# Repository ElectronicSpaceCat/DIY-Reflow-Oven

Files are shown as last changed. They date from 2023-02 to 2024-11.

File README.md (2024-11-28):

# DIY-Reflow-Oven
Firmware for running a PID controlled reflow oven

The toaster oven used in this project was the Black & Decker TO1785SG.

I was inpsired to make this project when I came across the https://www.rocketscream.com/blog/product/tiny-reflow-controller-v2/ controller while looking for a simple solution to building an oven myself.

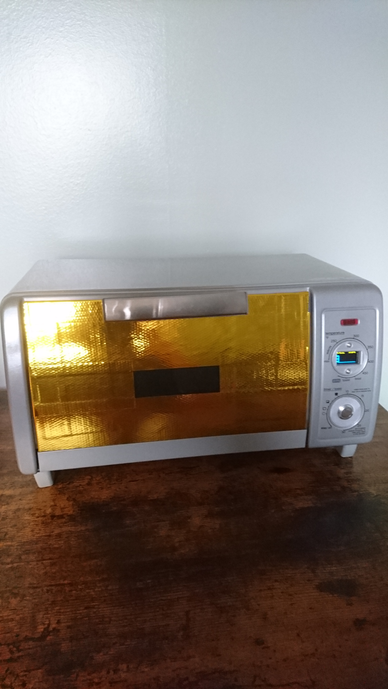
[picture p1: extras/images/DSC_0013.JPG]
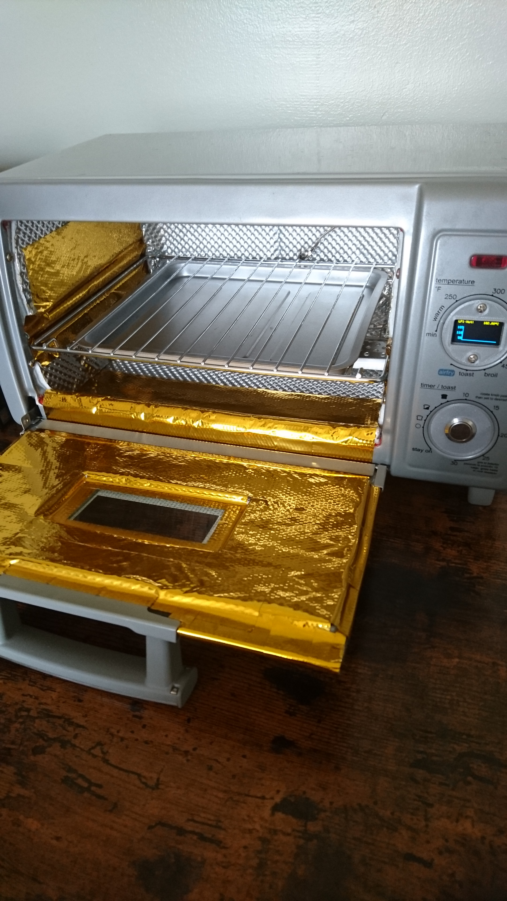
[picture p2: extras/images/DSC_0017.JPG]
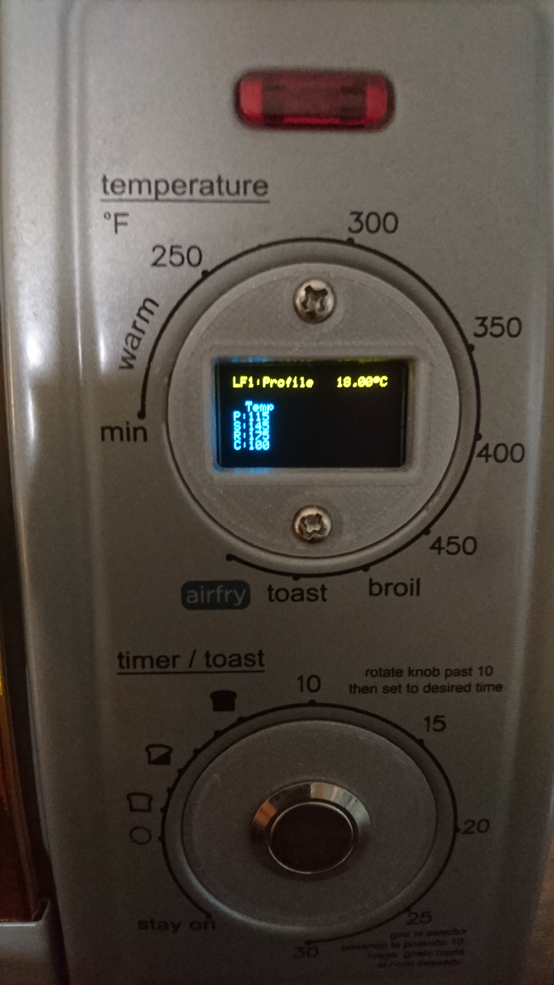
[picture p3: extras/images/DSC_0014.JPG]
  

Unfortunately the controllers were out of stock at the time so I ordered some of the parts like the OLED screen and SSRs to design my own implementation.

I chose to use an Arduino Mega 2560 Rev3 that I had laying around (finally had a use for it) and I wrote the firmware in C/C++ in Eclipse. I used a makefile from a Nordic nRF52 project to build it (to be independent of any IDE used). Note: The makefile will need to be modified depending on where your source files are located.

This reflow oven design has a single button for accessing/selecting reflow profiles and returning to the main screen.

A few toaster build guides:  
https://www.rocketscream.com/blog/forums/topic/reflow-oven-builds/  
https://www.whizoo.com/reflowoven

## Tools Needed
* Dremel or something to cut holes in the toaster
* 3d printer for the face plates

## Parts Used
* 1x Arduino Mega 2560 Rev3 (could likely port to other versions)  
https://store.arduino.cc/products/arduino-mega-2560-rev3

* 1x TO1785SG Toaster  
https://www.amazon.com/BLACK-DECKER-TO1785SG-Toaster-4-Slice/dp/B08R7WCRT8/ref=cm_cr_arp_d_product_top?ie=UTF8

* 1x Adafruit MCP9600  
https://www.amazon.com/Adafruit-4101-MCP9600-Thermocouple-Amplifier/dp/B07SZ8YVTW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

* 1x Alligator Clip K-Type Thermocouple Thermometer  
https://www.amazon.com/GenieFun-Alligator-Thermocouple-Thermometer-Temperature/dp/B01N11I90O

* 1x 6AN Weld on Bung Fitting (optional, but was used to run the thermocouple through the wall to the electronics side)  
https://www.amazon.com/EVIL-ENERGY-Fitting-Adapter-Stainless/dp/B089VP476L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

* 1x 7/16-20 Hex Jam Nut (for the weld bung)
https://www.amazon.com/16-20-Fine-Thread-Stainless-Steel/dp/B07QHFX87J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

* 1x Momentary Push Button Switch High Round Cap Waterproof Stainless Steel  
https://www.amazon.com/Waterproof-Momentary-Stainless-Button-Terminals/dp/B079HTQ7XD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

* 1x OLED 128x64 Pixel  
https://www.amazon.com/Hosyond-Display-Self-Luminous-Compatible-Raspberry/dp/B09C5K91H7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

* 3x SSR-40 AA (Kinda cheap (had a terminal break off), may want something better)  
1x each for the bottom element, top element, and fan (optional)  
https://www.amazon.com/SSR-40AA-80-250V-Output-24-380V-SSR-40/dp/B07FVDL7YX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

* 9VDC 1A Arduino Compatible Power Supply Adapter 110V AC (barrel jack needs to be cut off)
https://www.amazon.com/dp/B018OLREG4?th=1&psc=1&language=en_US

* Quick Connects (These things are amazing)  
https://www.amazon.com/Connectors-Conductor-Combination-Assortment-Connection/dp/B09CKDWK4Q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

* Reflect-A-GOLD   
https://www.designengineering.com/reflect-a-gold-heat-reflective-tape-2-x-15/

* Floor & Tunnel Shield II   
https://www.designengineering.com/floor-tunnel-shield-ii-21-x-24/

* Temperature Silicone Sealant   
https://www.amazon.co.uk/Weld-31314-Temperature-Silicone-Sealant/dp/B00ID8IUJY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

## Arduino Pinout
Refere to: ``` ./src/reflow_system.h ```

## How to use
* A short press at the main screen will start the reflow cycle. The temperature will be graphed over time and a vertical marker will indicated when it's in the next zone.
* Long press the button at the main screen to access the profile selecton screen. Once there, quick presses will cycle 1 of 5 hardcoded profiles.
Profiles can be modified in: ``` ./src/reflow_profiles.cpp ```
* Long press again to return to the main screen.
* Short press anytime during a cycle will abort it

## Screen Legend
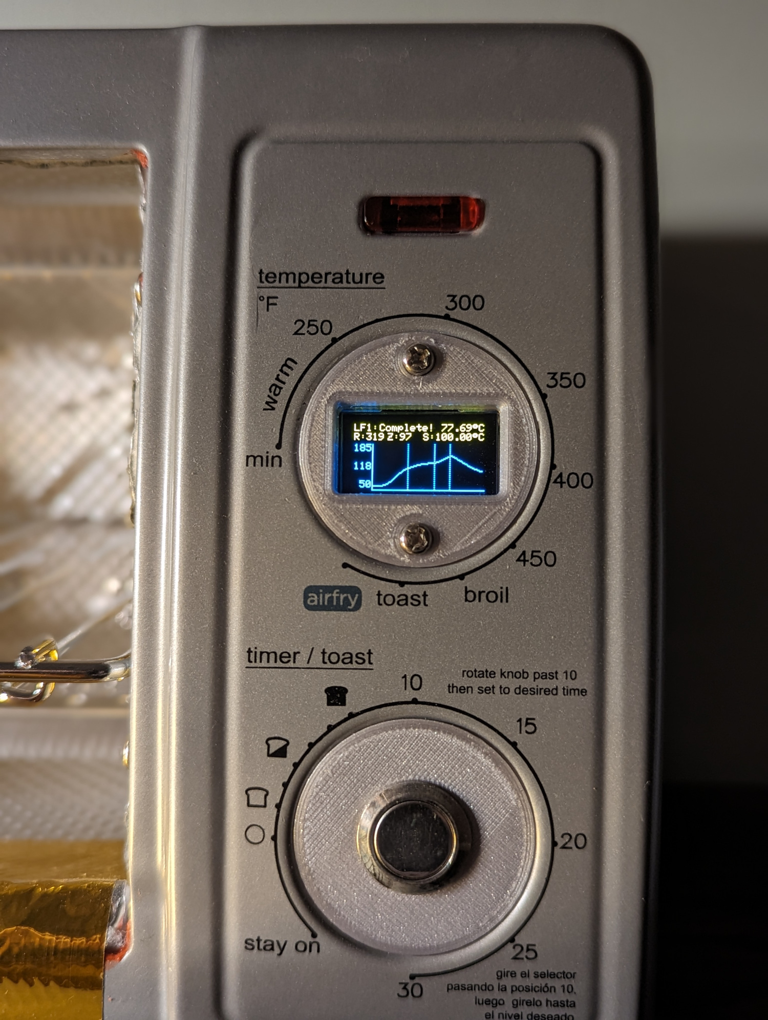
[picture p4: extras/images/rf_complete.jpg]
`  

From top left to top right (first line)  
<pre>
LF1       -  Lead Free Profile 1 (can modify but should keep it to 3 characters)  
Preheat   -  One of the states in: */src/reflow_state_machine.h >> state_t  
--.--C    -  Temperature read by the thermocouple  
</pre>

From bottom left to bottom right (second line)  
<pre>
R:--      -  Reflow time in seconds  
Z:--      -  Zone time in seconds  
S:---.--C -  Temperature setpoint for current zone
</pre>

## Compiling
#### Windows/Linux
* MinGW required for Windows to build, install instructions here: https://www.geeksforgeeks.org/installing-mingw-tools-for-c-c-and-changing-environment-variable/)
* Download the arm sdk to the project root folder from: https://developer.arm.com/downloads/-/gnu-rm
  * Windows: ```gcc-arm-none-eabi-10.3-2021.10-win32.zip```
  * Linux 32bit: ```gcc-arm-none-eabi-10.3-2021.10-x86_64-linux.tar.bz2```
  * Linux 64bit: ```gcc-arm-none-eabi-10.3-2021.10-aarch64-linux.tar.bz2```
* Clone to project root folder: https://github.com/arduino/ArduinoCore-sam.git
* Clone to project root folder: https://github.com/arduino/arduino-flash-tools.git
* Open command terminal: ```cd (path location here)/diy-reflow-oven```
* Run ```make```

  #### Update the following paths if needed:
  * ```./Makefile```:
    ```
    SDK_ROOT := $(PROJ_DIR)/ArduinoCore-sam
    SDK_TOOLS_ROOT := $(PROJ_DIR)/ArduinoCore-sam/packages/arduino/tools
    LINKER_DIR := $(SDK_ROOT)/variants/arduino_due_x/linker_scripts/gcc
    GNU_INSTALL_ROOT := $(PROJ_DIR)/gcc-arm-none-eabi-10.3-2021.10/bin/
    ```

## Flashing Firmware
  #### Windows
  * Run ```./usb_flash.bat``` and make sure to replace ```COM4``` with the correct port at the line  ```COMM_PORT := COM4```
  * The executable location in ```./usb_flash.bat``` can be modified at the line:
    ```
    $(PROJ_DIR)\arduino-flash-tools\tools_windows\bossac\bin
    ```
  #### Linux
  * Make sure the script is executable with ```sudo chmod +x usb_flash.sh```
  * Run ```./usb_flash.sh``` and make sure to replace ```ttyACM1``` with the correct port at the line ```COMM_PORT=ttyACM1```
  * Typically the port should be on ```ttyACM0``` or ```ttyACM1```
  * The executable location in ```./usb_flash.sh``` can be modified at the line:
    ```
    $(PROJ_DIR)\arduino-flash-tools\tools_linux_64\bossac\bin
    ```
  #### Notes
  * Precompiled binaries are also available at ```./build```
  * If the Adruino binary drag and drop flash method isn't broken like mine was then you may try that option instead.

## Debug/Testing
* Use a program like Putty to connect to the Arduino over USB at 115200 baud rate.  
* Type "help" to get a list of available commands.
* PID Tuning: Replace reflow_main.cpp with pid_tuner.cpp and recompile. Type "help" for available commands.
* The PID tuner is separate because it wasn't meant for reflow purposes. It was for recording the temperature ramp rates from room temp to the setpoint. Sadly, I lost spreadsheet with some of my test data. However, one can set Putty to record the output window and save it as a csv file, which the debug output is already formatted for it.

## TODO
* schematic
* more images

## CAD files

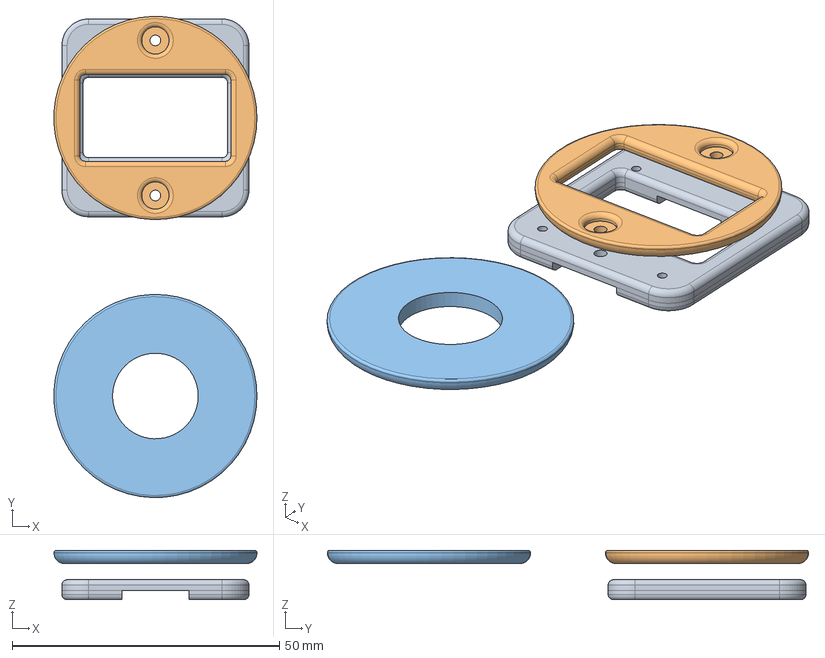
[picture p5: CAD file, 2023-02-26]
extras/cad/FreeCad/covers.FCStd
38.0 x 90.0 x 9.25 mm

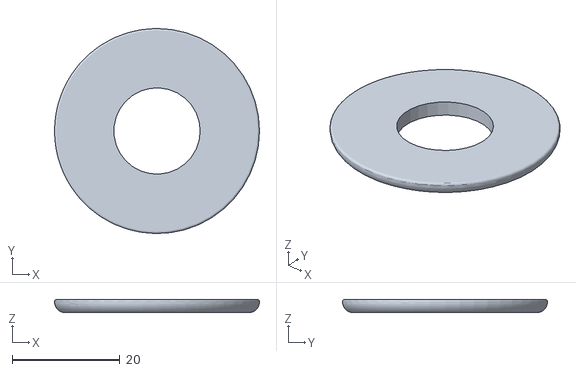
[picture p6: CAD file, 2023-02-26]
extras/cad/FreeCad/button_cover.obj
38.0 x 38.0 x 2.50

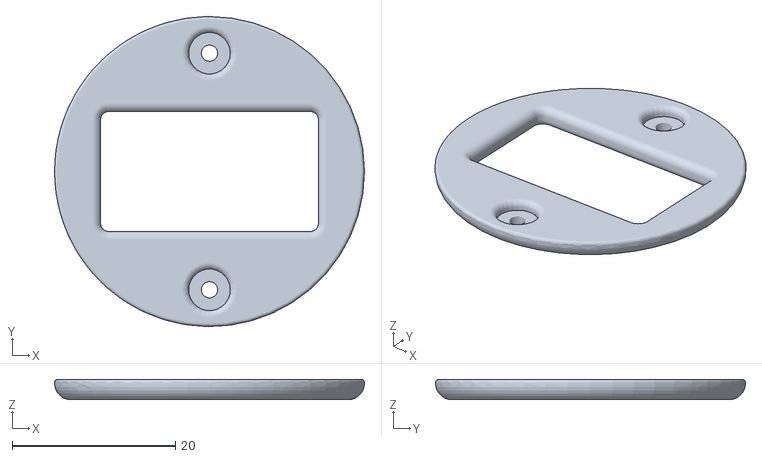
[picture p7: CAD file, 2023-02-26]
extras/cad/FreeCad/oled_front.obj
38.0 x 38.0 x 2.50

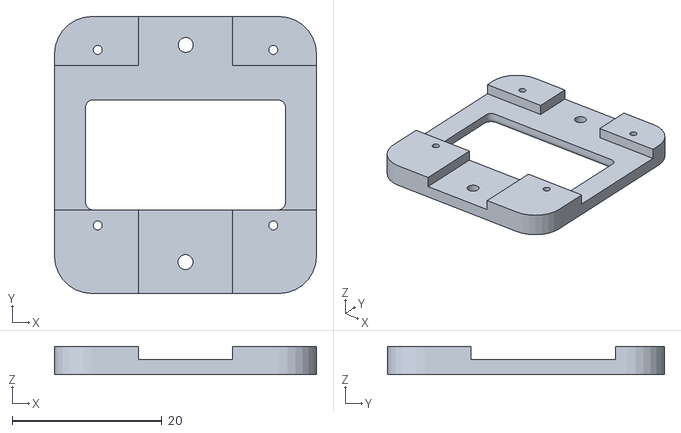
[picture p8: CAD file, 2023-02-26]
extras/cad/FreeCad/oled_back.obj
35.0 x 37.0 x 3.75

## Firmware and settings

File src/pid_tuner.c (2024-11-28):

/*******************************************************************************
    MIT License

    Copyright (c)  2021-present  Andrew Green

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
 *******************************************************************************/

/**
 * NOTE: This file is meant to replace reflow_debug.cpp for testing purposes.
 *
 *       It allows fine tuning of the PID controller.
 */


#include "reflow_debug.h"
#include "reflow_profiles.h"
#include "reflow_state_machine.h"
#include "reflow_thermocouple.h"
#include "reflow_system.h"
#include "reflow_pid.h"

#define INTERVAL_TIME 1000

#define DEBUG_OUTPUT
//#define DEBUG_TEMP

#ifdef DEBUG_OUTPUT
#define DEBUG_PRINT_CSV_DATA
#undef DEBUG_TEMP
#endif

typedef enum {
  DATA_PID_SETPOINT = 0, DATA_PID_KP, DATA_PID_KI, DATA_PID_KD, NUM_DATA_ENTRIES
} data_entry_t;

static bool _debugMode = false;
static double _setpoint, _kp, _ki, _kd = 0;

static unsigned long timerDebug;
static bool printHeader = true;
static char cmd[50];
static data_entry_t dataEntry = NUM_DATA_ENTRIES;

static void printDebug(void);
static void readCmds(void);
static void processCmd(void);
static void printHelp(void);
static void processDataEntry(void);

namespace REFLOW::DEBUG {

  void init(void) {
    timerDebug = millis();
    Serial.begin(115200);
  }

  void poll(void) {
    // Time to read print debug data?
    if((millis() - timerDebug) >= INTERVAL_TIME) {
      // Update next time to read thermocouple
      timerDebug += INTERVAL_TIME;
      printDebug();
    }
    // Process any user commands
    readCmds();
  }

  bool getDebugMode(void) {
    return _debugMode;
  }

}

void printDebug(void) {
  using namespace REFLOW;
#ifdef DEBUG_TEMP
    Serial.print("HJ: "); Serial.print(thermocouple.readThermocouple()); Serial.print(" ");
    Serial.print("CJ: "); Serial.print(thermocouple.readAmbient()); Serial.print(" ");
    Serial.print("ADC: "); Serial.print(thermocouple.readADC() * 2); Serial.println(" uV");
    // Flush the serial buffer
    Serial.flush();
#else
#ifdef DEBUG_PRINT_CSV_DATA
  // If reflow process is on going
  if(SM::getStatus() == SM::STATUS_ON) {
    if(printHeader == true) {
      printHeader = false;
      Serial.println(F("ReflowTime,Setpoint,Input,Output"));
    }
    // Send temperature and time stamp to serial
    Serial.print(SM::get_timerReflow());
    Serial.print(F(","));
    Serial.print(PID::getPID_setPoint());
    Serial.print(F(","));
    Serial.print(PID::getPID_input());
    Serial.print(F(","));
    Serial.println(PID::getPID_output());
  }
  else {
    printHeader = true;
  }
#endif
#endif
}

static void readCmds(void) {
  using namespace REFLOW;
  static unsigned int idx = 0;
  if(Serial.available()) {
    char locChr = Serial.read();
    // Line feed or carriage return?
    if(locChr == 0x0A || locChr == 0x0D) {
      // Yes - Add null terminator and process command
      cmd[idx] = '\0';
      processCmd();
      // Reset index
      idx = 0;
    }
    else if(idx < sizeof(cmd)) {
      cmd[idx++] = locChr;
    }
    else {
      idx = 0;
    }
  }
}

static void processCmd(void) {
  using namespace REFLOW;

  // Process commands

  /// PRINT COMMANDS
  if(!strcmp(cmd, "help")) {
    printHelp();
  }
  /// TOGGLE RUN MODE
  else if(!strcmp(cmd, "debug")) {
    // Toggle debug mode
    if(_debugMode == true){
      _debugMode = false;
      
      Serial.println(">> debug mode disabled");
    }
    else {
      _debugMode = true;
      Serial.println(">> debug mode enabled");
      Serial.println("");
      printHelp();
    }
  }
  else if(!strcmp(cmd, "start")) {
    if(SM::getState() == SM::STATE_IDLE){
      SM::setStartSignal();
      Serial.println(">> running");
    }
  }
  else if(!strcmp(cmd, "stop")) {
    SM::setStartSignal();
    Serial.println(">> stopped");
  }
  /// FAN ON
  else if(!strcmp(cmd, "fan on")) {
    if(SM::getState() == SM::STATE_IDLE){
      SYSTEM::ssrFanON();
      Serial.println(">> fan on");
    }
  }
  /// FAN OFF
  else if(!strcmp(cmd, "fan off")) {
    if(SM::getState() == SM::STATE_IDLE){
      SYSTEM::ssrFanOFF();
      Serial.println(">> fan off");
    }
  }
  /// HEATER TOP ON
  else if(!strcmp(cmd, "heater top on")) {
    if(SM::getState() == SM::STATE_IDLE){
      SYSTEM::ssrHeaterTopON();
      Serial.println(">> heater top on");
    }
  }
  /// HEATER TOP OFF
  else if(!strcmp(cmd, "heater top off")) {
    if(SM::getState() == SM::STATE_IDLE){
      SYSTEM::ssrHeaterTopOFF();
      Serial.println(">> heater top off");
    }
  }
  /// HEATER BOTTOM ON
  else if(!strcmp(cmd, "heater bottom on")) {
    if(SM::getState() == SM::STATE_IDLE){
      SYSTEM::ssrHeaterBottomON();
      Serial.println(">> heater bottom on");
    }
  }
  /// HEATER BOTTOM OFF
  else if(!strcmp(cmd, "heater bottom off")) {
    if(SM::getState() == SM::STATE_IDLE){
      SYSTEM::ssrHeaterBottomOFF();
      Serial.println(">> heater bottom off");
    }
  }
  /// SET SETPOINT
  else if(!strcmp(cmd, "setpoint")) {
    dataEntry = DATA_PID_SETPOINT;
    Serial.print(">> enter temp setpoint: ");
  }
  /// SETS PID KP
  else if(_debugMode == true && !strcmp(cmd, "kp")) {
    dataEntry = DATA_PID_KP;
    Serial.print(">> enter kp: ");
  }
  /// SETS PID KI
  else if(_debugMode == true && !strcmp(cmd, "ki")) {
    dataEntry = DATA_PID_KI;
    Serial.print(">> enter ki: ");
  }
  /// SETS PID KD
  else if(_debugMode == true && !strcmp(cmd, "kd")) {
    dataEntry = DATA_PID_KD;
    Serial.print(">> enter kd: ");
  }
  /// GET TERMS
  else if(_debugMode == true && !strcmp(cmd, "get pid")) {
    Serial.print("PID: ");
    Serial.print(_kp);
    Serial.print(", ");
    Serial.print(_ki);
    Serial.print(", ");
    Serial.println(_kd);
  }
  /// GET TEMPERATURES
  else if(!strcmp(cmd, "get temps")) {
    Serial.print("TC: ");
    Serial.print(THERMOCOUPLE::getTemperature());
    Serial.print(", Amb: ");
    Serial.println(THERMOCOUPLE::getTemperatureAmbient());
  }
  else if(dataEntry != NUM_DATA_ENTRIES) {
    if(_debugMode) {
      processDataEntry();
    }
  }
  else {
    Serial.println(">> unknown command");
  }
}
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

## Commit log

2023-02-26 added cad files for button and oled housing
    [Reflow profile calculator.ods, button_cover.obj, covers.FCStd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]
2023-09-02 added reflow complete image, removed unused sheets from spreadsheet
    [Reflow profile calculator.ods]
2023-09-02 reduced cool-zone setpoint temperature on LF1-4 to 50 so the pid wouldn't kick on the heater elements
